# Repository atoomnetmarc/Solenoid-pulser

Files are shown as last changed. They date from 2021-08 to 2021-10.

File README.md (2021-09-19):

# Status

Prototype. Circuit has been validated and know to work on a breadboard, but have not been made into a pcb yet.

# Ding!?

This circuit charges a 2200uF capacitor with a 100 ohm resistor and pulses a 12V JF-0530B solenoid for about 15ms with a NE555 timer chip. The NE555 is configured as a non-retriggerable one-shot timer where the length of the trigger pulse does not matter. The solenoid will strike a reception desk bell to produce a ding sound. The 100 ohm resistor limits triggering to a maximum of once per second. Add a 6mm bushing to the solenoid axle to shorten its throw.

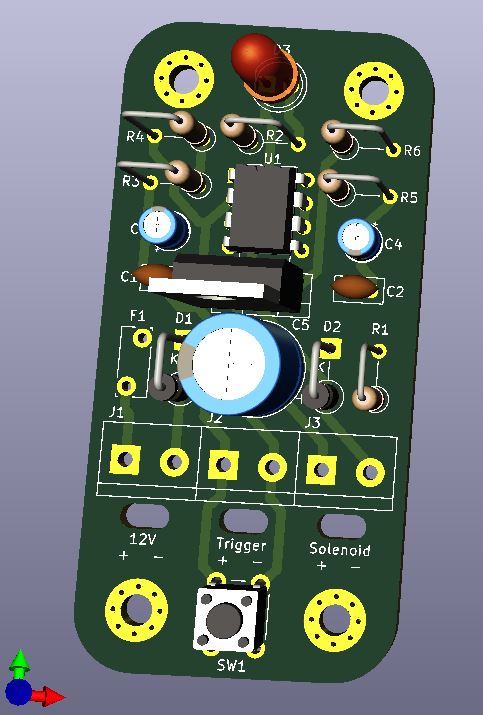
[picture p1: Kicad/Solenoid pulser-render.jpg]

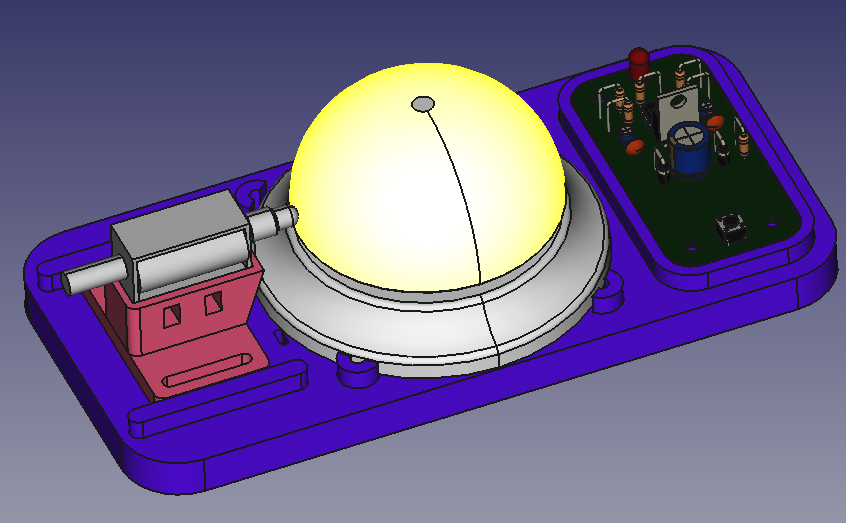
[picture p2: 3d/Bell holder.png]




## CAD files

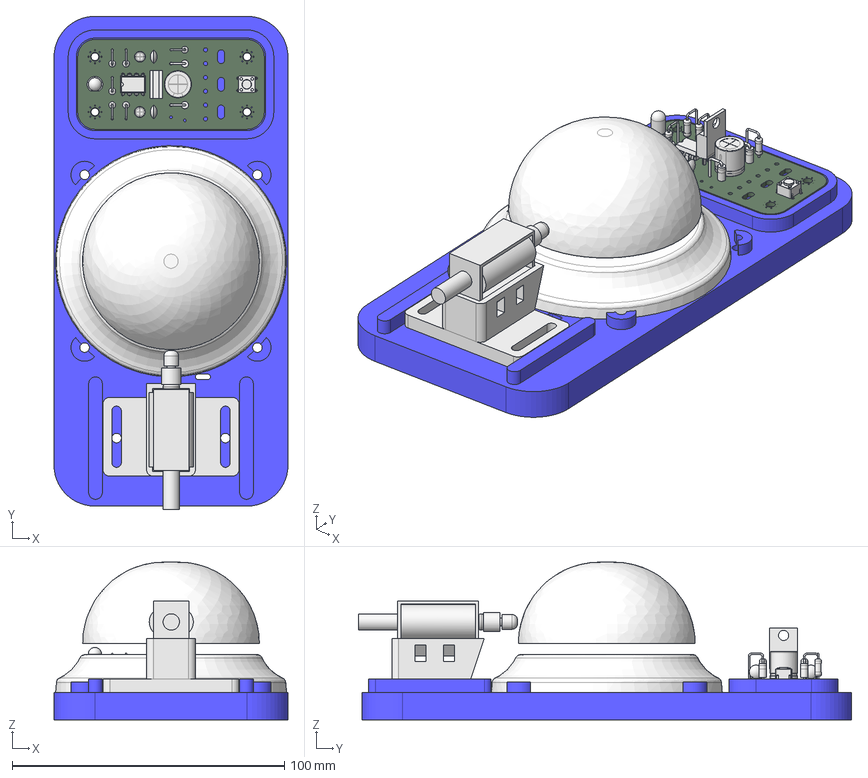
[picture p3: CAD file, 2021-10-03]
3d/Bell holder.FCStd
86.0 x 181.3 x 58.0 mm
base
bell
axle-extra-spacer
solenoid-body
solenoid-axle
axle-rubber-spacer
solenoid holder

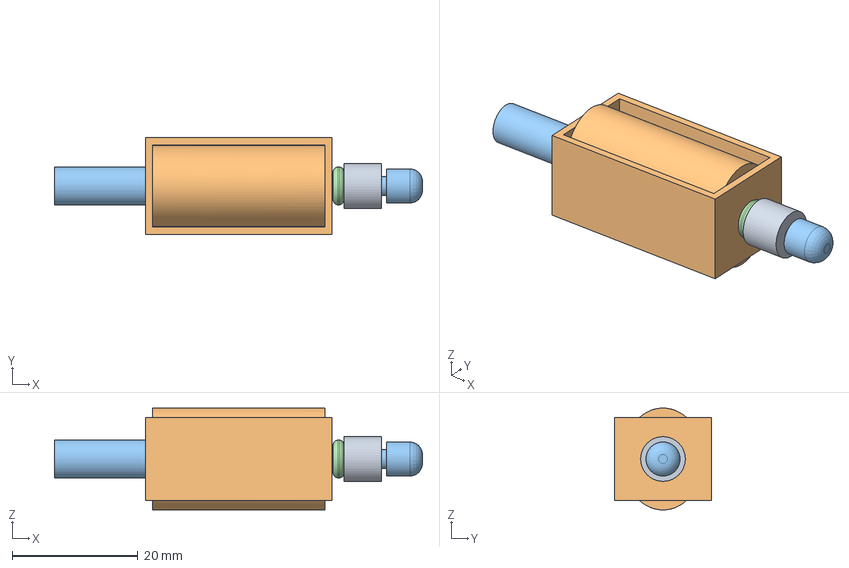
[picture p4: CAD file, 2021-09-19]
3d/Parts/solenoid with spacer.step
58.5 x 15.4 x 16.2 mm
axle-extra-spacer
solenoid-body
solenoid-axle
axle-rubber-spacer

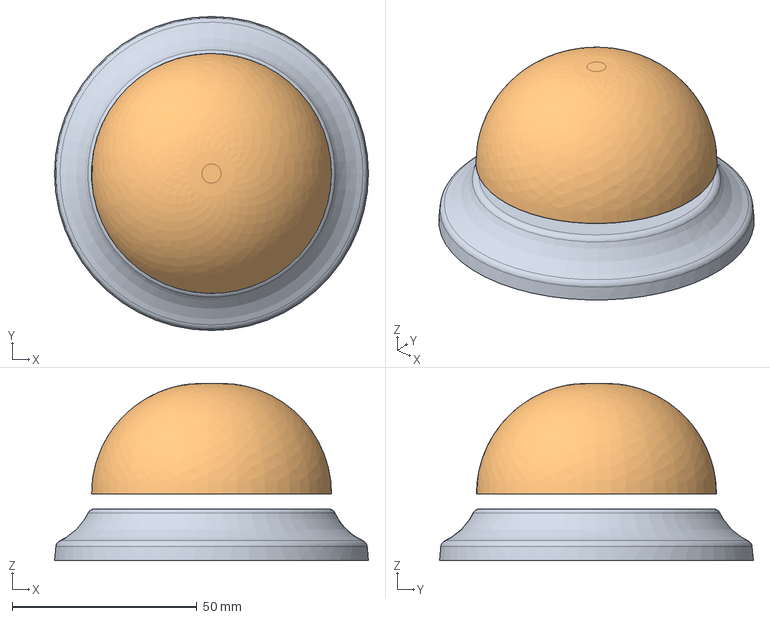
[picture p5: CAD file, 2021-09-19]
3d/Parts/desk bell 8.5cm.step
85.0 x 85.0 x 48.0 mm
base
bell

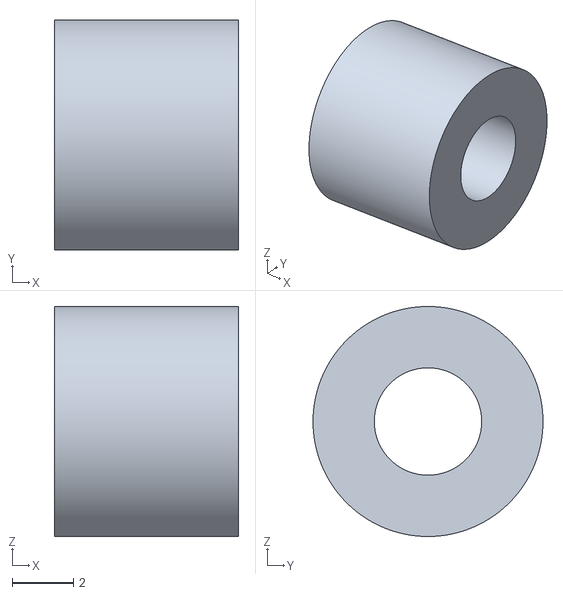
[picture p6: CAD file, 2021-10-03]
3d/solenoid axle extra spacer.stl
6.00 x 7.50 x 7.50

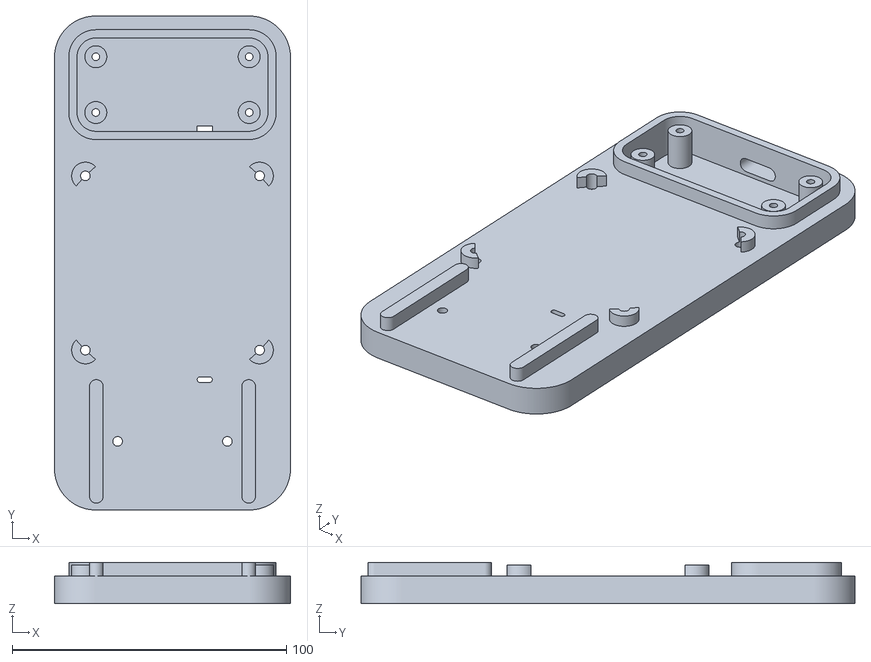
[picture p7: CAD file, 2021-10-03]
3d/base plate.stl
86.0 x 180.0 x 15.0

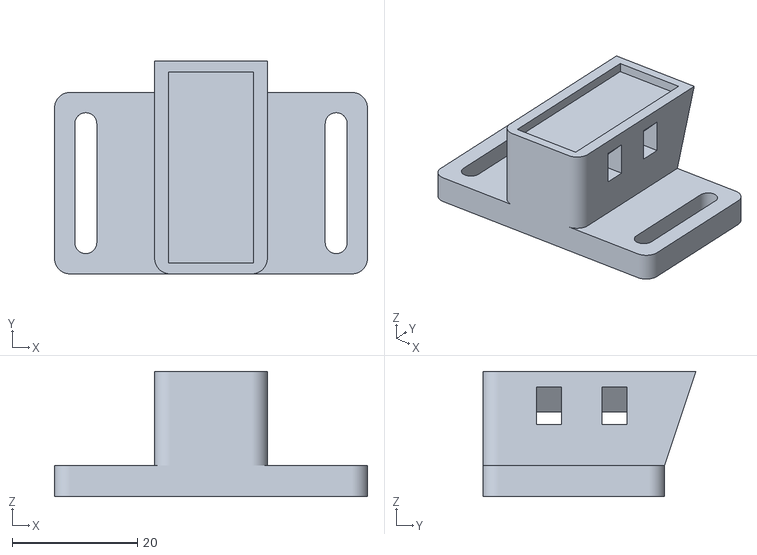
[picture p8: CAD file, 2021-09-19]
3d/solenoid holder.stl
50.0 x 34.0 x 20.0

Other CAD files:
3d/Parts/Solenoid with spacer.FCStd
3d/Parts/desk bell 8.5cm.FCStd

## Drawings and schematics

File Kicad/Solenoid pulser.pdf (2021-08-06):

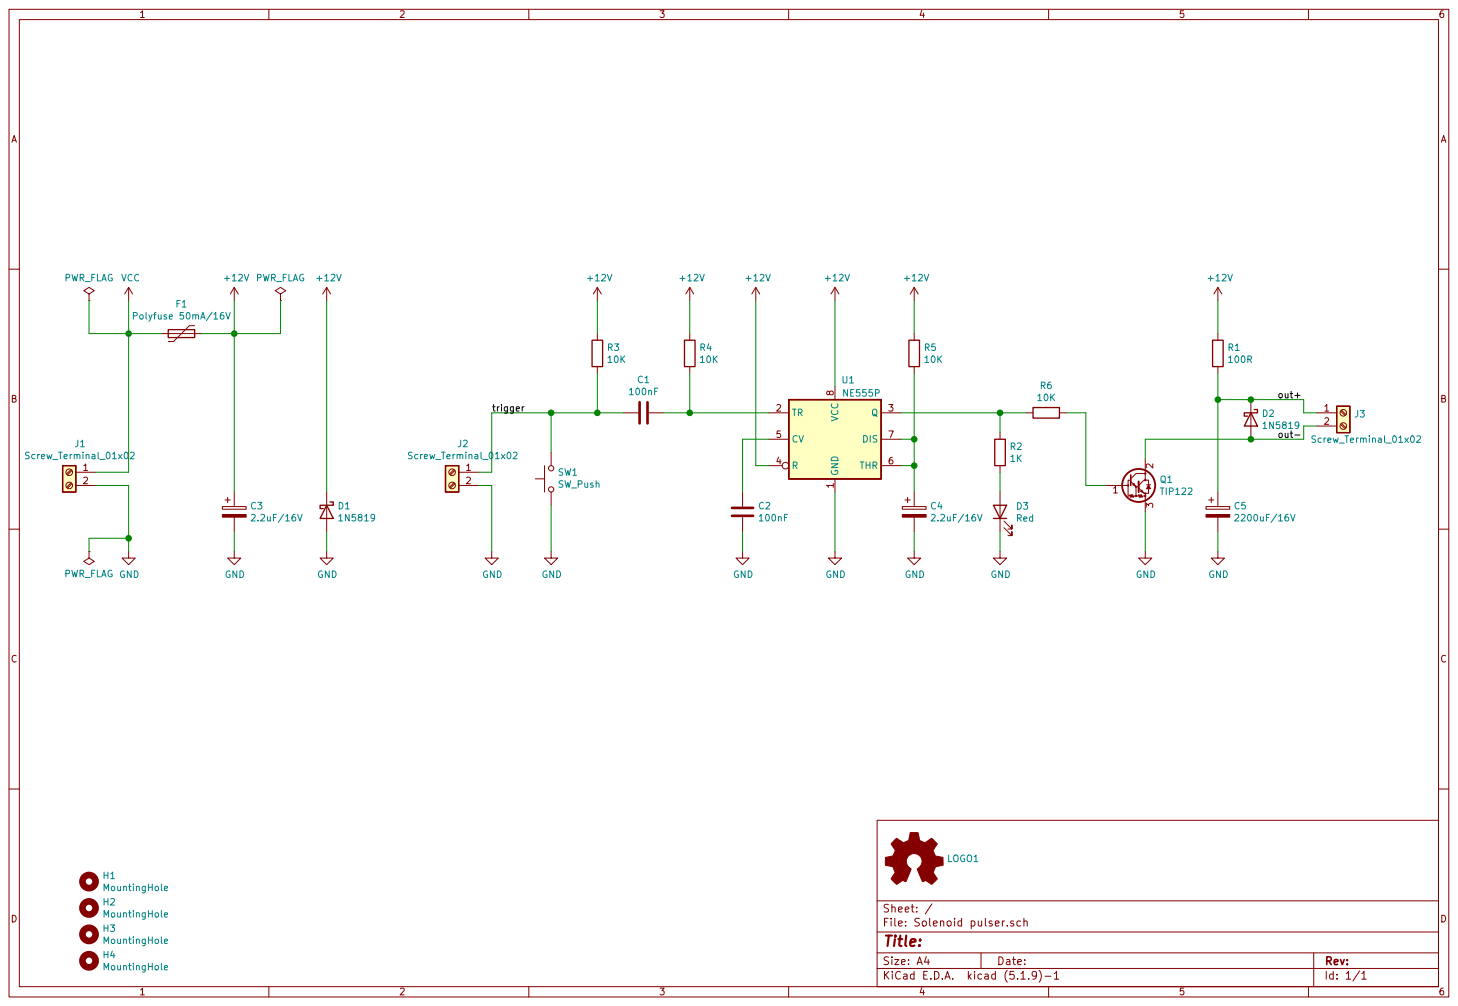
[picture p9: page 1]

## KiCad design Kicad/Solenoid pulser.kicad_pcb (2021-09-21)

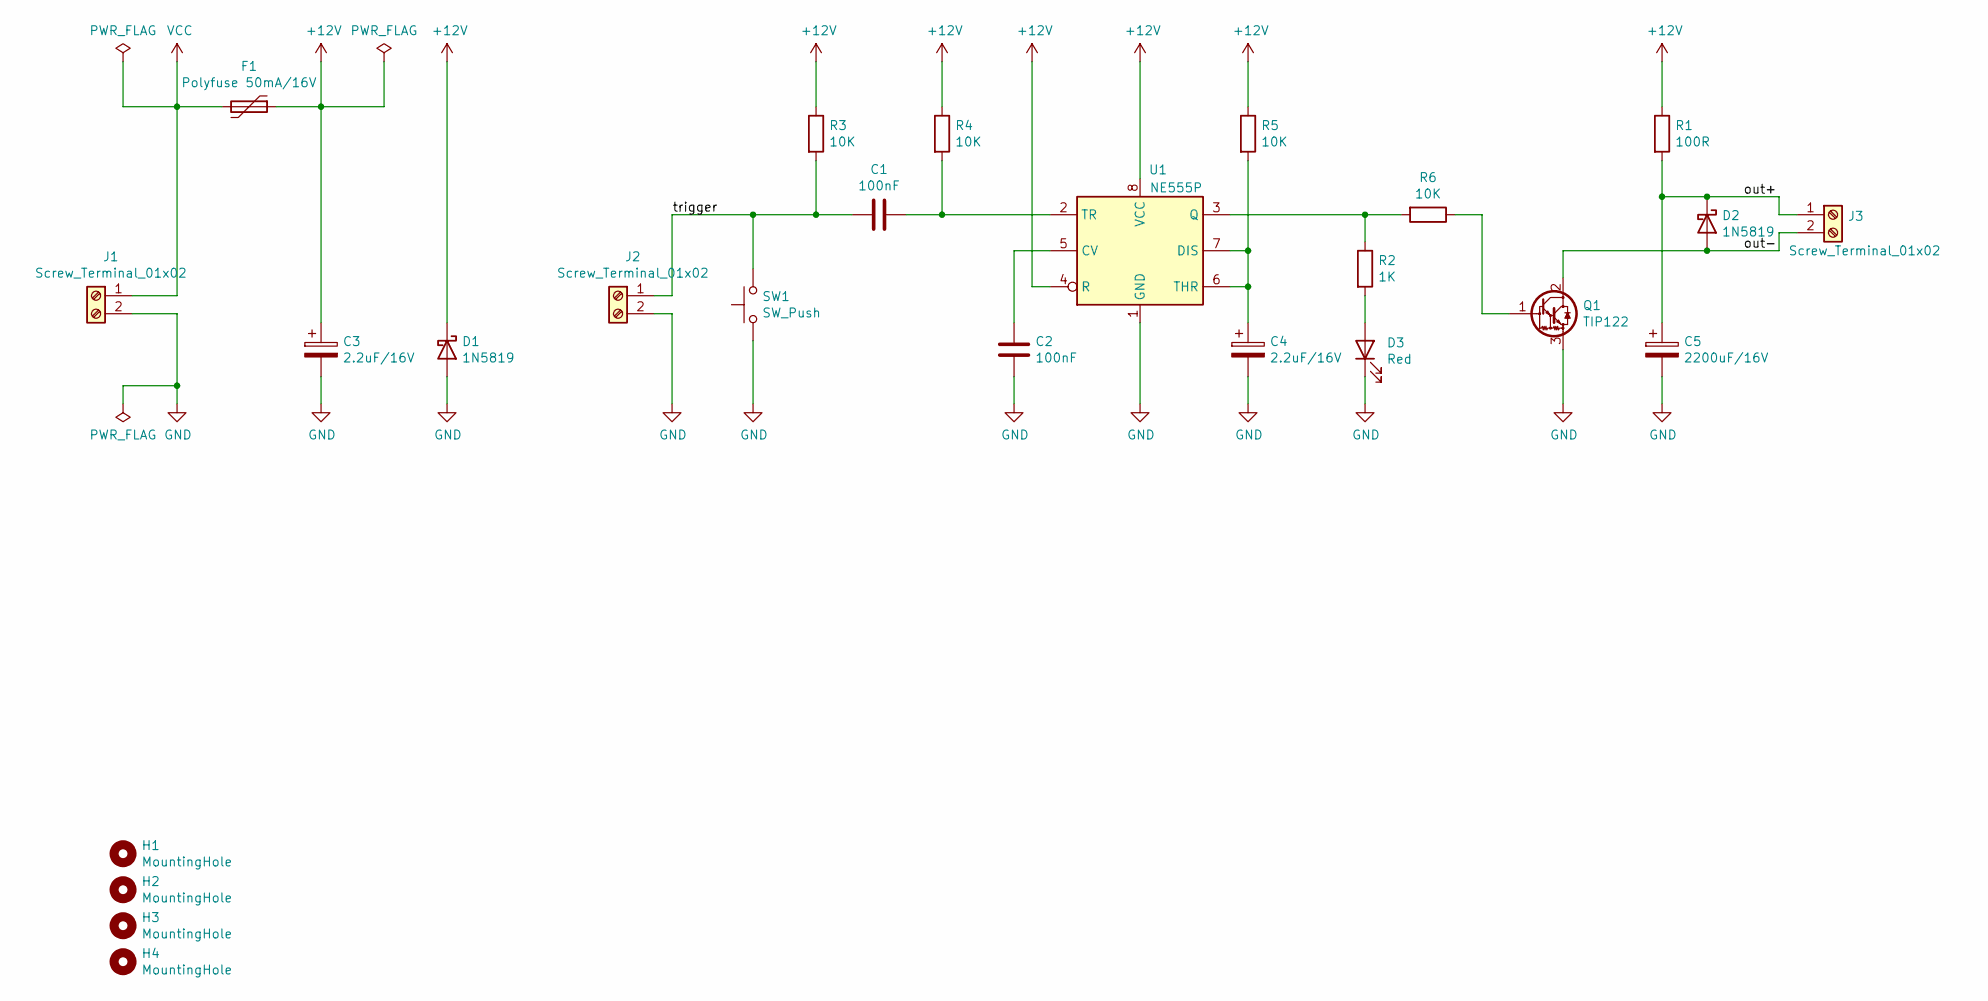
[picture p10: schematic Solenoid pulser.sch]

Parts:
C1, C2: 100nF; C_Disc_D5.0mm_W2.5mm_P2.50mm
C3, C4: 2.2uF/16V; CP_Radial_D4.0mm_P2.00mm
C5: 2200uF/16V; CP_Radial_D10.0mm_P5.00mm
D1, D2: 1N5819; D_DO-41_SOD81_P5.08mm_Vertical_KathodeUp
D3: Red; LED_D5.0mm
F1: Polyfuse 50mA/16V; Fuse_Bourns_MF-RG300
H1, H2, H3, H4: MountingHole; MountingHole_3.2mm_M3_Pad_Via
J1, J2, J3: Screw_Terminal_01x02; TerminalBlock_bornier-2_P5.08mm
Q1: TIP122; TO-220-3_Vertical
R1: 100R; R_Axial_DIN0207_L6.3mm_D2.5mm_P5.08mm_Vertical
R2: 1K; R_Axial_DIN0207_L6.3mm_D2.5mm_P5.08mm_Vertical
R3, R4, R5, R6: 10K; R_Axial_DIN0207_L6.3mm_D2.5mm_P5.08mm_Vertical
SW1: SW_Push; SW_PUSH_6mm
U1: NE555P; DIP-8_W7.62mm

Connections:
+12V: C3.1, D1.1 (K), F1.1, R1.1, R3.1, R4.1, R5.1, U1.4 (R), U1.8 (VCC)
/out+: C5.1, D2.1 (K), J3.1, R1.2
/out-: D2.2 (A), J3.2, Q1.2 (C)
/trigger: C1.2, J2.1, R3.2, SW1.2
GND: C2.2, C3.2, C4.2, C5.2, D1.2 (A), D3.1 (K), J1.2, J2.2, Q1.3 (E), SW1.1, U1.1 (GND)
unnamed: C1.1, R4.2, U1.2 (TR)
unnamed: C2.1, U1.5 (CV)
unnamed: C4.1, R5.2, U1.6 (THR), U1.7 (DIS)
unnamed: D3.2 (A), R2.2
unnamed: Q1.1 (B), R6.1
unnamed: R2.1, R6.2, U1.3 (Q)
VCC: F1.2, J1.1

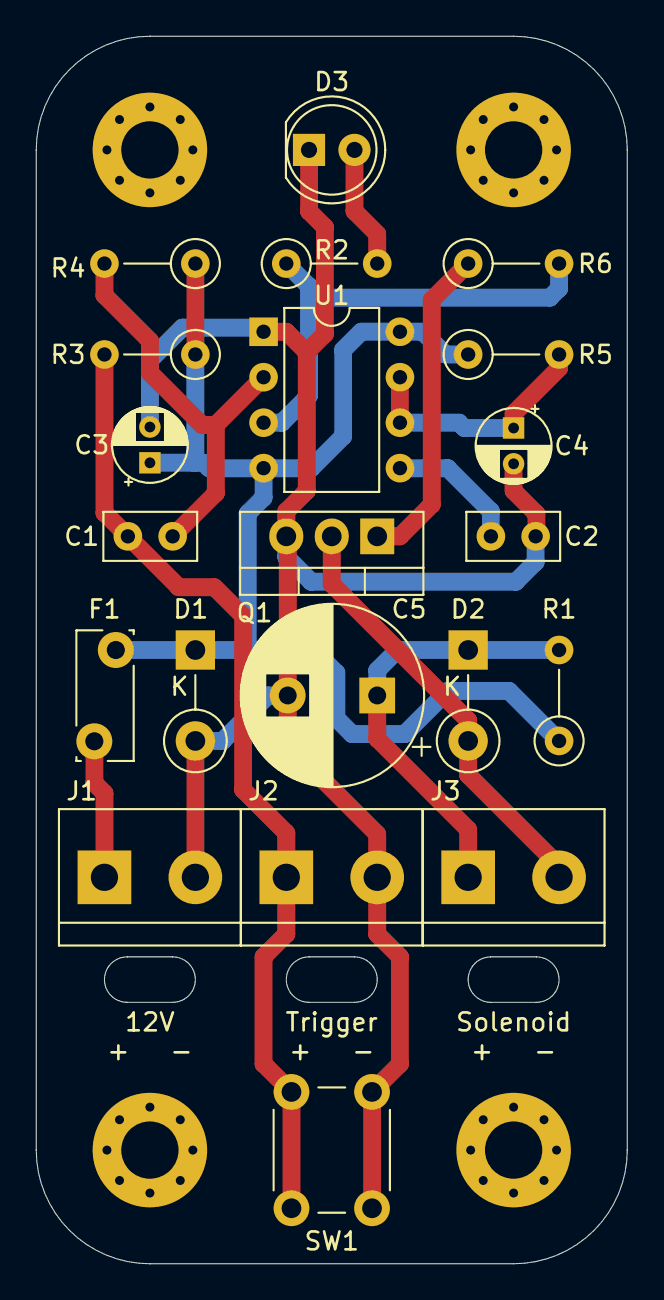
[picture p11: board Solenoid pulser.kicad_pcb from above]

Board: 2 copper layers, 33.0 x 68.6 mm, 25 parts (0 on the bottom side), 12 nets.

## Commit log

2021-08-06 Initial commit.
    [Solenoid pulser-B_Cu.gbl, Solenoid pulser-B_Mask.gbs, Solenoid pulser-B_Paste.gbp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]
2021-09-19 First try 3d design bell holder.
    [Bell holder.FCStd, Solenoid pulser.step, Solenoid with spacer.FCStd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]
2021-09-19 Added example assembly.
2021-09-20 Tweak pcb and 3d design.
    [Bell holder.FCStd, Solenoid pulser.kicad_pcb, Solenoid pulser.sch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]
2021-09-21 Generate gerber and BOM.
    [Solenoid pulser-B_Cu.gbl, Solenoid pulser-B_Mask.gbs, Solenoid pulser-B_Paste.gbp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]
2021-10-03 Tweak screw hole diameter.
    [Bell holder.FCStd, base plate.stl]
2021-10-03 Tweak spacer hole diameter.
    [Bell holder.FCStd, Solenoid with spacer.FCStd, solenoid axle extra spacer.stl]

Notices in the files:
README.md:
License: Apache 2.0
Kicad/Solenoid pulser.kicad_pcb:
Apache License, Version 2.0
